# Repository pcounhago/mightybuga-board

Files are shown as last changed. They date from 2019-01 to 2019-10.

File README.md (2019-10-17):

# Mighty Bug-A Control board

Control board for the line follower racing car project designed at [A Industriosa](https://intranet.aindustriosa.org/).

## Releases

Version | Description | Status
------------ | ------------- | ------------
[v1](v1/README.md) | Initial board design. Has a mayor supply problem with the AMS1117-3.3 regulator. **Do not use unless you replace the regulator with a more capable one.** | Released
[v1.1](v1.1/README.md) | Updated version of v1 that solves the supply problems by replacing the regulator with a MP2307DN. | Released
[v2](v2/README.md) | Lighter version of the v1.1 redesigned to improve weight distribution in the car. | Released
[v2.1](v2.1/README.md) | Even lighter version of the control board. Include SWIO interface for programming and debug purposes. Fix some minor issues found in v2. | Released

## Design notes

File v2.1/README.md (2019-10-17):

# Mighty Bug-A Board v2.1

Control board for the line follower racing car project designed at [A Industriosa](https://intranet.aindustriosa.org/).

* Check the 3D printed chassis designs at [https://gitlab.com/punkto/line_follower_3d_designs](https://gitlab.com/punkto/line_follower_3d_designs)

* For the firmware refer to [https://github.com/hmightypirate/AllMyCircuits](https://github.com/hmightypirate/AllMyCircuits)

## Description

Designed to control a line follower racing car based on differential drive, this board includes an STM32F103 microcontroller coupled with a TB6612FNG dual channel motor driver and a U3V12F9 step-up regulator to power two Pololu micro metal gearmotors at stable 9V. The board provides headers to connect the motors using the magnetic encoder boards mounted on them.

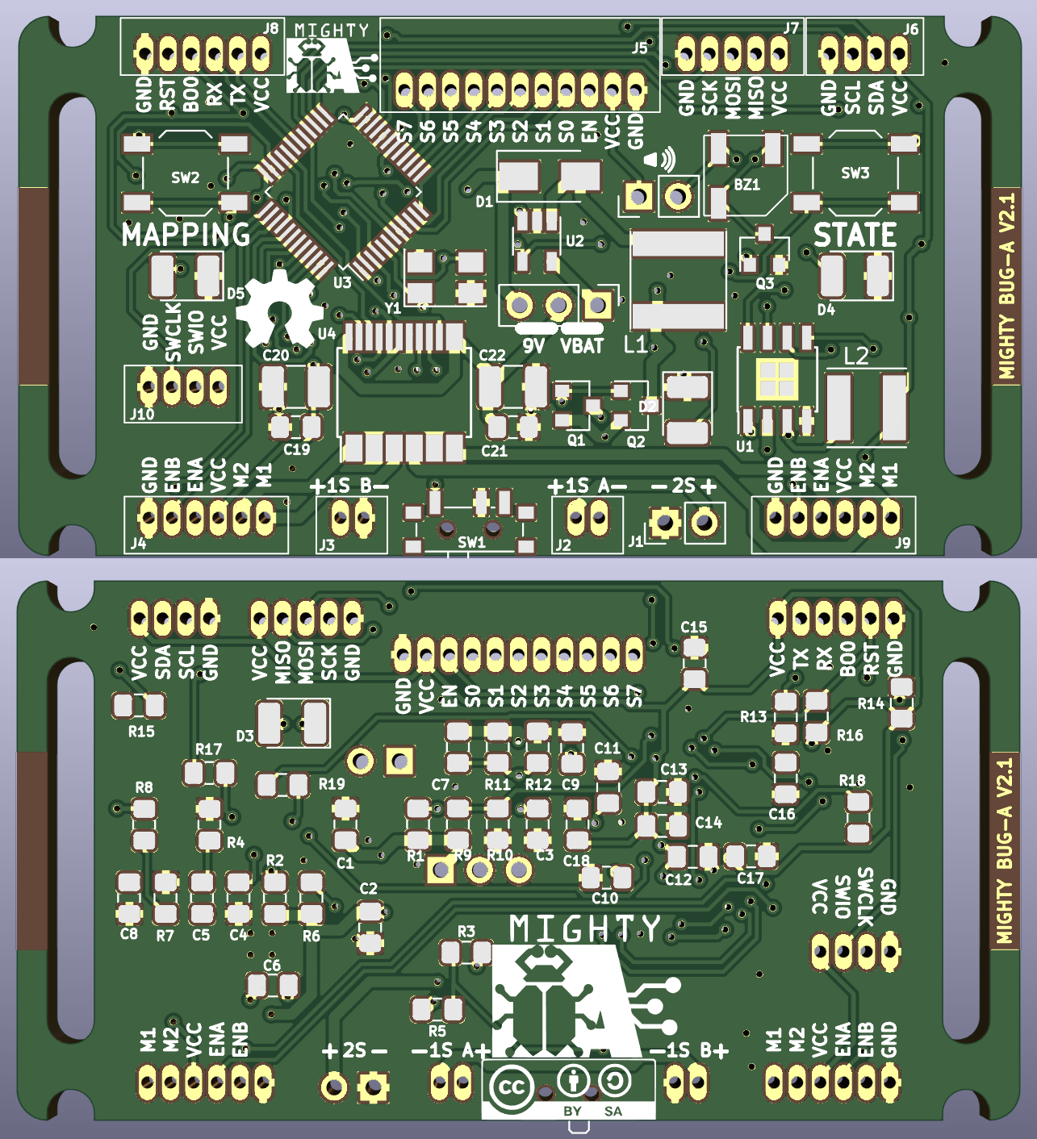
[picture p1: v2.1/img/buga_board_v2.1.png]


To detect the position of the line, a QTR-8A array featuring 8 Fairchild QRE1113 reflectance sensors is connected to the right angle header mounted on the front.

2 LEDs, 2 push buttons and a buzzer are provided to configure the board and give feedback while the car is on the track.

There is also a UART header that can be used to program the microcontroller and to establish a communication link through cable or Bluetooth if an HC-05 adapter is used.

To expand the capabilities of the board, I2C and SPI buses are available on a header so that other hardware (like an IMU or a slave microcontroller) can be added at any time.

## BOM

Reference | Description | Quantity
------------ | ------------- | ------------- |
BZ1 | MLT-5020 SMD buzzer | 1
C1, C14 | 0805 ceramic capacitor, 1uF | 2
C10, C11 | 0805 ceramic capacitor, 20pF | 2
C12, C13, C15, C16, C17, C19, C21 | 0805 ceramic capacitor, 100nF | 7
C2 | 0805 ceramic capacitor, 10uF | 1
C20, C22 | 0805 ceramic capacitor, 10uF | 2
C3 | 0805 ceramic capacitor, 56nF | 1
C4 | 0805 ceramic capacitor, 100pF | 1
C5 | 0805 ceramic capacitor, 3.9nF | 1
C6 | 10nF | 1
C7 | 15pF | 1
C8 | 22uF | 1
C9, C18 | 4.7uF | 2
D1 | B220A-13-F | 1
D2 | 1210 Green LED | 1
D3 | 1N4148 1210 diode | 1
D4 | 1210 Red LED | 1
D5 | 1210 Blue LED | 1
J1, JP2 | 2 pin 2.54mm vertical header | 2
J2, J6, J7 | JST B6B-ZR connector | 3
J3 | JST S11B-ZR | 1
J4 | JST B4B-ZR | 1
J5 | B5B-ZR | 1
JP1 | 3 pin 2.54mm straight header | 1
L1 | Taiyo Yuden_NR-60xx 4.7uH inductor | 1
L2 | Taiyo Yuden NR-50xx 10uH inductor | 1
Q1, Q2 | SI2369DS P-Channel 30V MOSFET, SOT-23 | 2
Q3 | S8050 NPN Transistor, SOT-23 | 1
R1, R6, R7, R9, R10, R13, R14, R15, R16, R19 | 0805 Resistor, 10k | 10
R11 | 0805 Resistor, 47k | 1
R12 | 0805 Resistor, 7.5k | 1
R17, R18 | 0805 Resistor, 100 | 2
R2, R3, R5, R20 | 0805 Resistor, 100K | 4
R4 | 0805 Resistor, 6.8k | 1
R8 | 0805 Resistor, 26.1k | 1
SW1 | PCM12 SPDT switch | 1
SW2, SW3 | TL3343 Push button | 2
U1 | MP2307DN | 1
U2 | SC4503 | 1
U3 | STM32F103C8T6 | 1
U4 | TB6612FNG | 1
Y1 | 5032 8Mhz crystal | 1

## Acknowledgements

This work was inspired by the great job done in the micromouse maze solving robot Bulebule by [Bulebots](https://github.com/Bulebots):

[https://github.com/Bulebots/bulebule](https://github.com/Bulebots/bulebule)

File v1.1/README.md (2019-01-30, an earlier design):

# Mighty Bug-A Board v1.1

Control board for the line follower racing car project designed at [A Industriosa](https://intranet.aindustriosa.org/).

* Check the 3D printed chassis designs at [https://gitlab.com/punkto/line_follower_3d_designs](https://gitlab.com/punkto/line_follower_3d_designs)

* For the firmware refer to [https://github.com/hmightypirate/AllMyCircuits](https://github.com/hmightypirate/AllMyCircuits)

## Description

Designed to control a line follower racing car based on differential drive, this board includes an STM32F103 microcontroller coupled with a TB6612FNG dual channel motor driver and a U3V12F9 step-up regulator to power two Pololu micro metal gearmotors at stable 9V. The board provides headers to connect the motors using the magnetic encoder boards mounted on them.

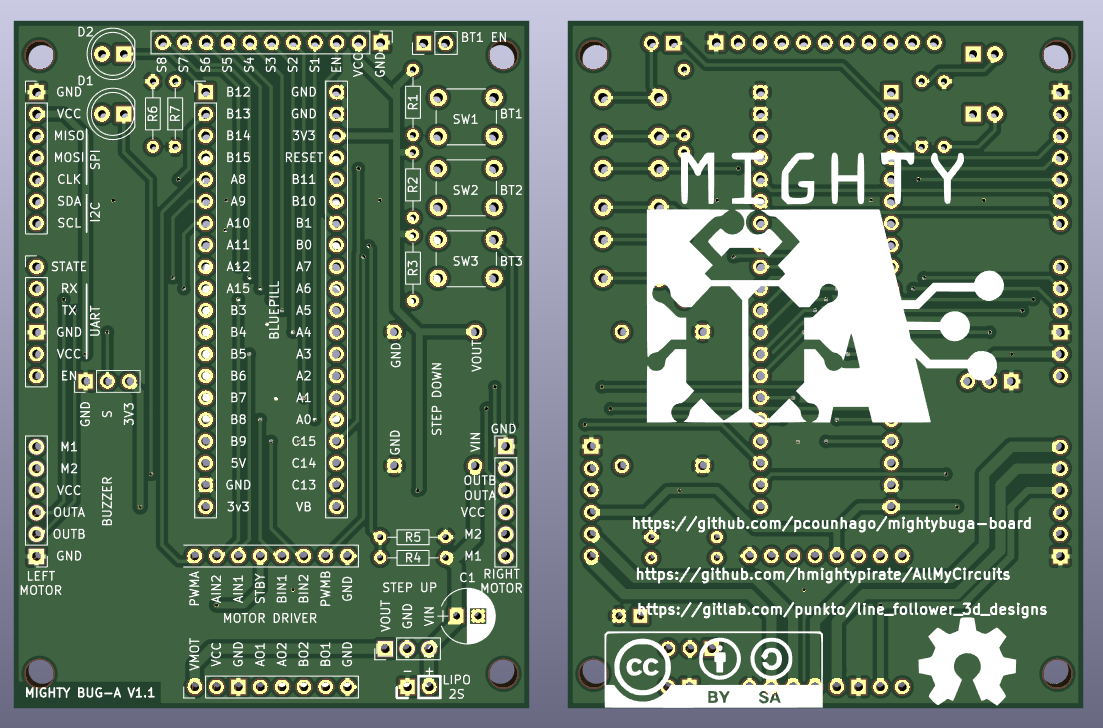
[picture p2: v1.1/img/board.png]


To detect the position of the line, a QTR-8A array featuring 8 Fairchild QRE1113 reflectance sensors is connected to the right angle header mounted on the front.

2 LEDs, 3 push buttons and a buzzer are provided to configure the board and give feedback while the car is on the track.

There is also a UART header that can be used to program the microcontroller and to establish a communication link through cable or Bluetooth if an HC-05 adapter is used.

To expand the capabilities of the board, I2C and SPI buses are available on a header so that other hardware (like an IMU or a slave microcontroller) can be added at any time.

**This board solves the problem with the regulator found in the previous version. By replacing the AMS1117-3.3 with a MP2307DN, the board can easily handle the regulation from the 8.4V provided by the battery when fully charged to the 3.3V required by the electronics.**

## BOM

Item | Description | Quantity
------------ | ------------- | ------------- |
Bluepill | STM32F103 microcontroller board | 1
MP2307DN | 3.3V Step-down voltage regulator. Can be found with the name Mini-360 in chinese stores. | 1
U3V12F9 | 9V Step-up regulator board from Pololu | 1
Buzzer | Passive buzzer board | 1
TB6612FNG | 2 Channel motor driver board | 1
5 mm LED | 5mm LEDs of different colors | 2
Push button | Through hole push buttons | 3
100Ω Resistor | Through hole resistors | 5
47kΩ Resistor | Through hole resistors | 1
20kΩ Resistor | Through hole resistors | 1
40x1 Female socket 2.54mm pitch | Female socket to plug, the bluepill, the motor driver and the Bluetooth module to the board | 1
40x1 Male pin 2.54mm pitch | Male pin strip to plug the motors, the battery, the expansion boards and the jumper to the board | 1
40x1 Right angle male pin 2.54mm pitch | Male pin strip to connect the reflectance sensor array to the board | 1
33uF Capacitor | Electrolytic capacitor to connect to the output of the step up regulator | 1

## Acknowledgements

This work was inspired by the great job done in the micromouse maze solving robot Bulebule by [Bulebots](https://github.com/Bulebots):

[https://github.com/Bulebots/bulebule](https://github.com/Bulebots/bulebule)

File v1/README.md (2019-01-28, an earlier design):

# Mighty Bug-A Board v1

Control board for the line follower racing car project designed at [A Industriosa](https://intranet.aindustriosa.org/).

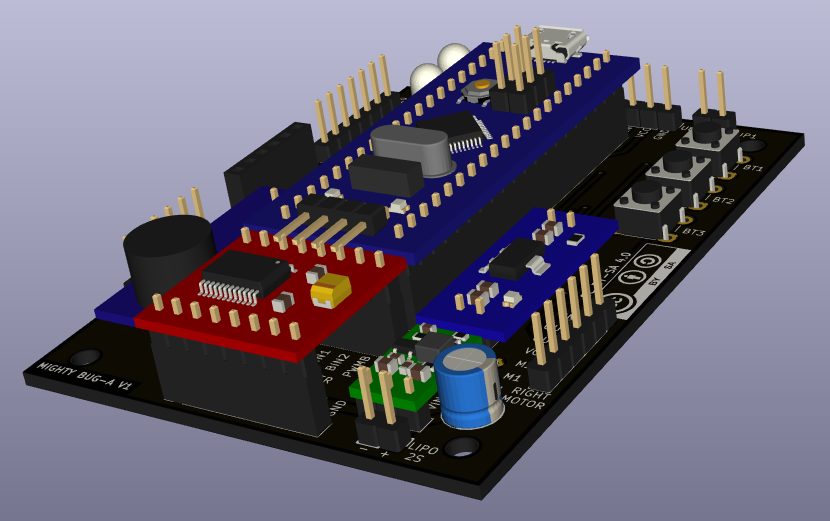
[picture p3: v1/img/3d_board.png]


* Check the 3D printed chassis designs at [https://gitlab.com/punkto/line_follower_3d_designs](https://gitlab.com/punkto/line_follower_3d_designs)

* For the firmware refer to [https://github.com/hmightypirate/AllMyCircuits](https://github.com/hmightypirate/AllMyCircuits)

## Warning!

**This board is made public here just for documentation purposes but its use in new designs is not recommended.** There is a major design flaw that makes the board burn when too much current is drawn. The step down regulator (AMS1117-3.3) can source up to 800 mA as stated in its datasheet. The problem is that the max output current is greatly affected by the difference between the input and output voltages. In this case The power source is a 2S lipo battery that provides 8.4V when fully charged. When converting this voltage down to 3.3V to power all the electronics, a lot of power is dissipated in the regulator making it burn when too much current is demanded.

**This issue is fixed in version v1.1 that can also be found in this repository.**

## Description

Designed to control a line follower racing car based on differential drive, this board includes an STM32F103 microcontroller coupled with a TB6612FNG dual channel motor driver and a U3V12F9 step-up regulator to power two Pololu micro metal gearmotors at stable 9V. The board provides headers to connect the motors using the magnetic encoder boards mounted on them.

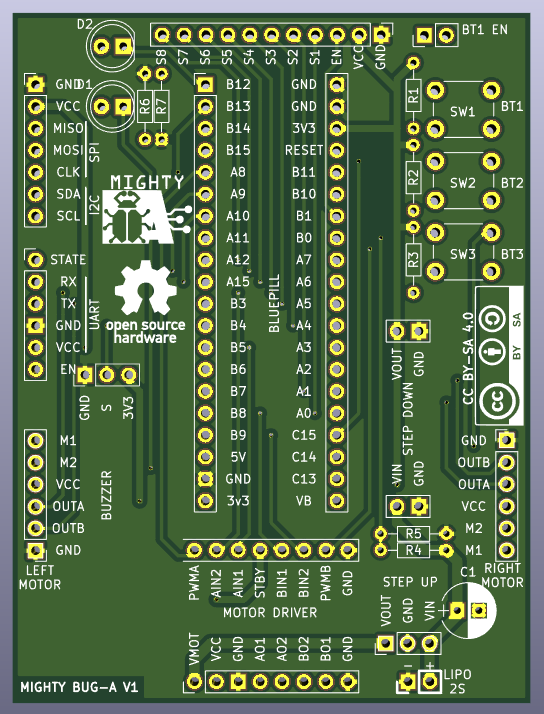
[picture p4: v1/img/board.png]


To detect the position of the line, a QTR-8A array featuring 8 Fairchild QRE1113 reflectance sensors is connected to the right angle header mounted on the front.

2 LEDs, 3 push buttons and a buzzer are provided to configure the board and give feedback while the car is on the track.

There is also a UART header that can be used to program the microcontroller and to establish a communication link through cable or Bluetooth if an HC-05 adapter is used.

To expand the capabilities of the board, I2C and SPI buses are available on a header so that other hardware (like an IMU or a slave microcontroller) can be added at any time.

## BOM

Item | Description | Quantity
------------ | ------------- | ------------- |
Bluepill | STM32F103 microcontroller board | 1
AMS1117-3.3 | 3.3V Step-down voltage regulator | 1
U3V12F9 | 9V Step-up regulator board from Pololu | 1
Buzzer | Passive buzzer board | 1
TB6612FNG | 2 Channel motor driver board | 1
5 mm LED | 5mm LEDs of different colors | 2
Push button | Through hole push buttons | 3
100Ω Resistor | Through hole resistors | 5
47kΩ Resistor | Through hole resistors | 1
20kΩ Resistor | Through hole resistors | 1
40x1 Female socket 2.54mm pitch | Female socket to plug, the bluepill, the motor driver and the Bluetooth module to the board | 1
40x1 Male pin 2.54mm pitch | Male pin strip to plug the motors, the battery, the expansion boards and the jumper to the board | 1
40x1 Right angle male pin 2.54mm pitch | Male pin strip to connect the reflectance sensor array to the board | 1
33uF Capacitor | Electrolytic capacitor to connect to the output of the step up regulator | 1

## Acknowledgements

This work was inspired by the great job done in the micromouse maze solving robot Bulebule by [Bulebots](https://github.com/Bulebots):

[https://github.com/Bulebots/bulebule](https://github.com/Bulebots/bulebule)

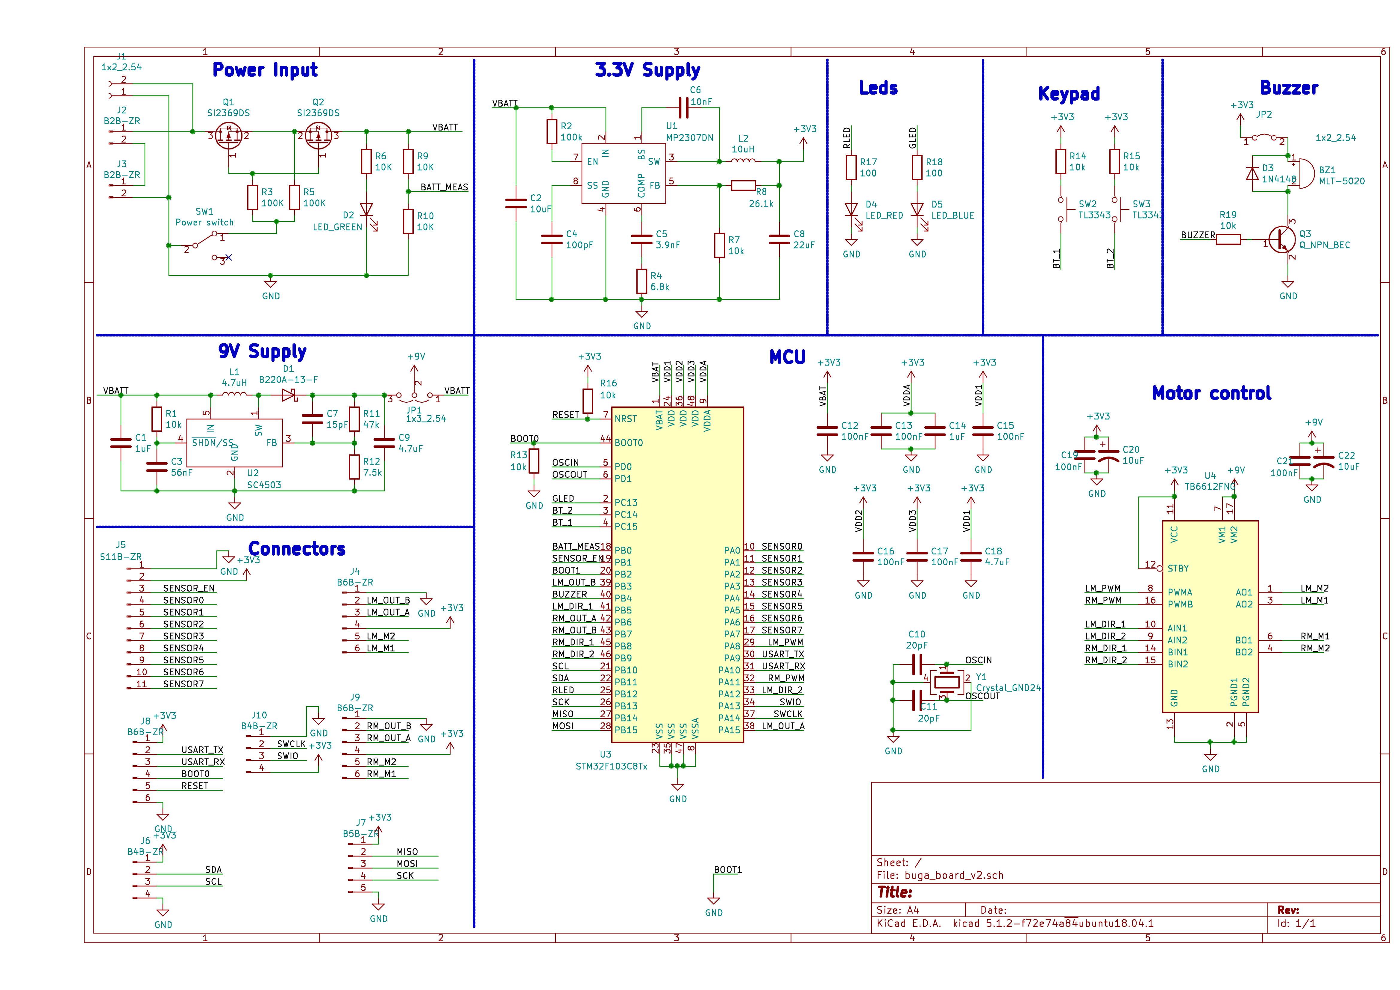
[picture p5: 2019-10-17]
v2.1/buga_board_v2-schematic.png

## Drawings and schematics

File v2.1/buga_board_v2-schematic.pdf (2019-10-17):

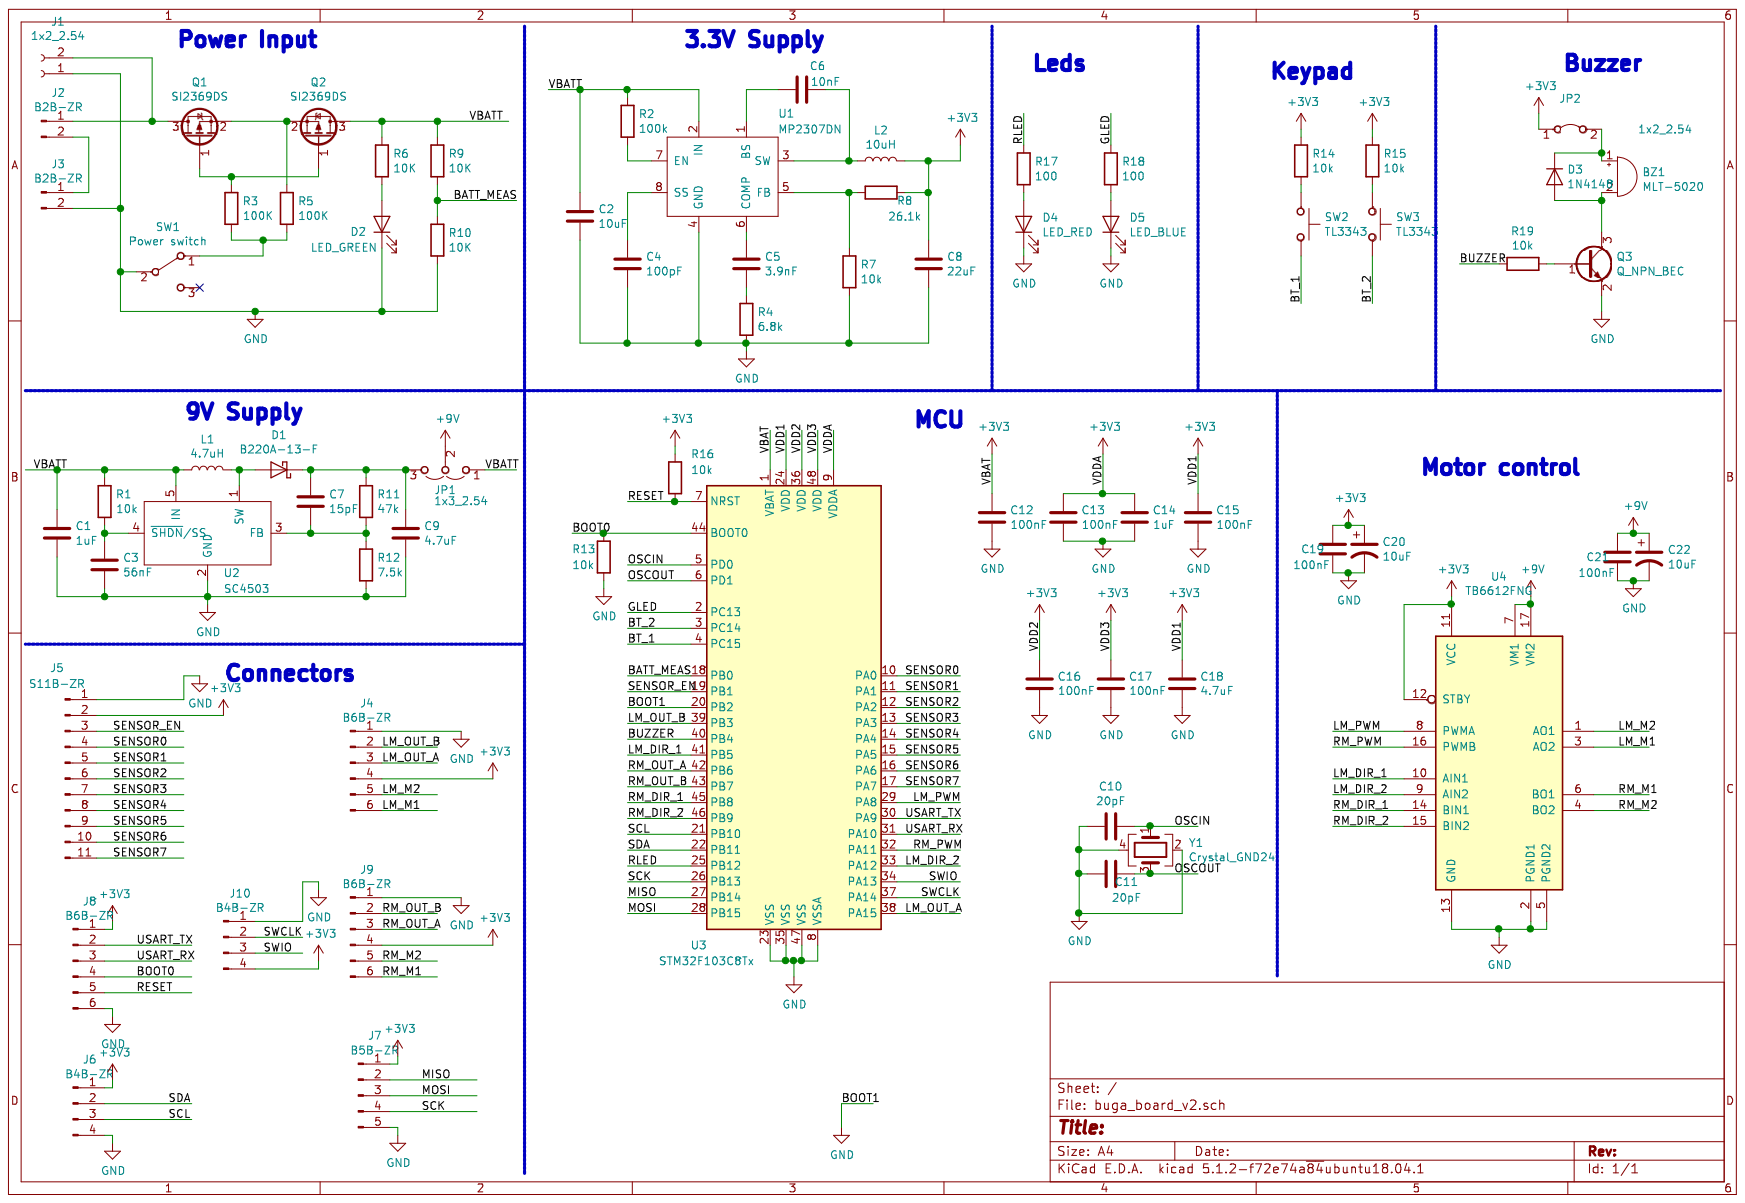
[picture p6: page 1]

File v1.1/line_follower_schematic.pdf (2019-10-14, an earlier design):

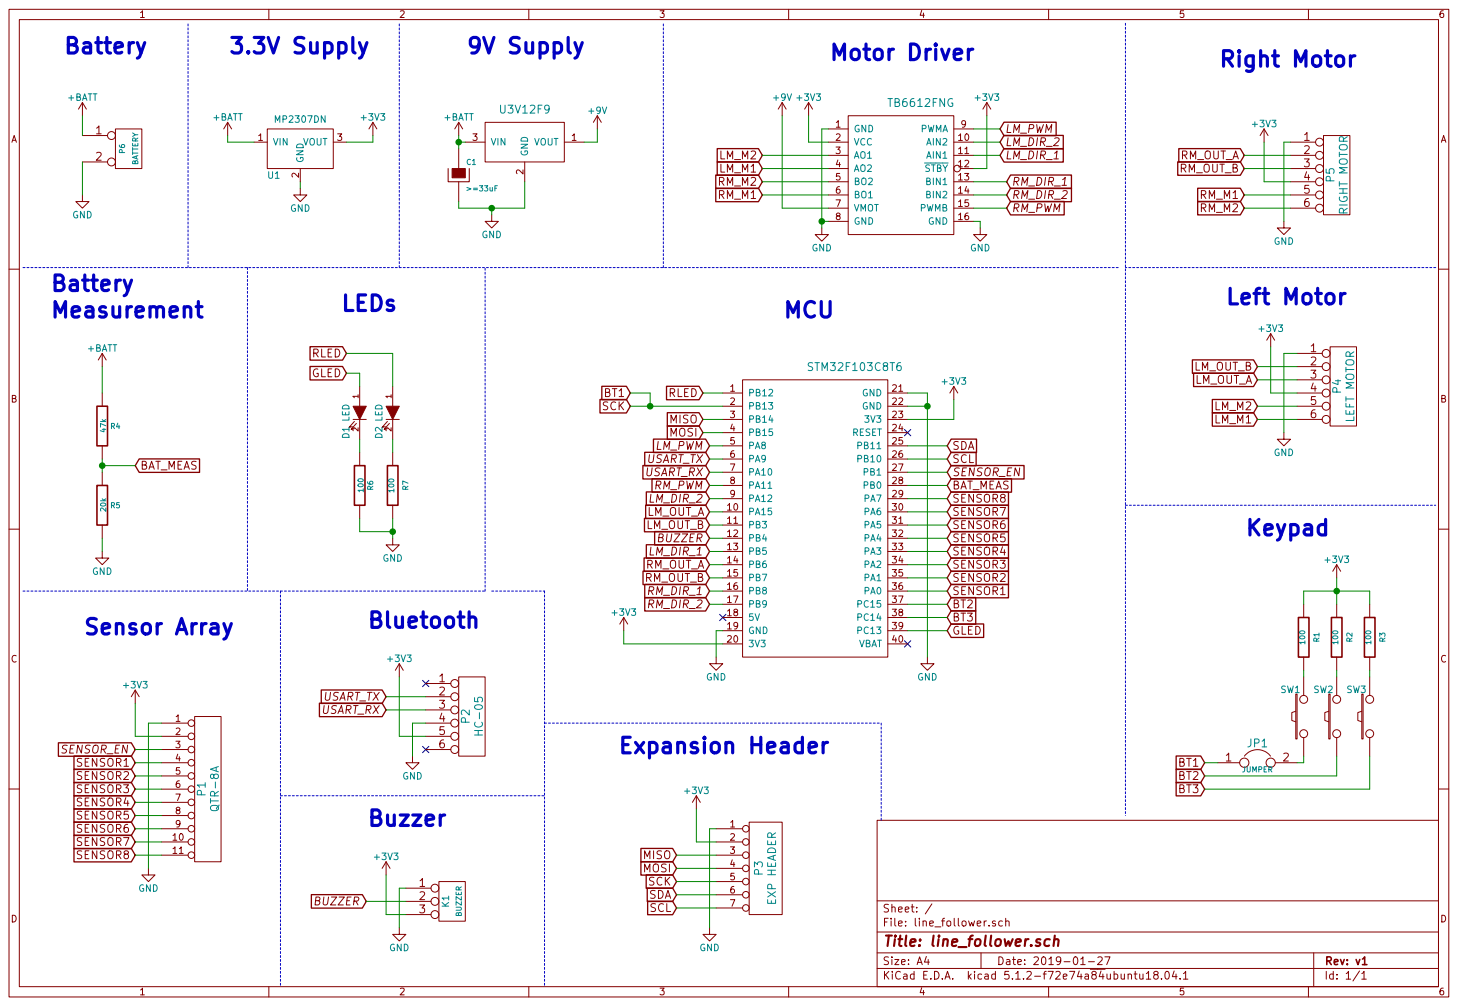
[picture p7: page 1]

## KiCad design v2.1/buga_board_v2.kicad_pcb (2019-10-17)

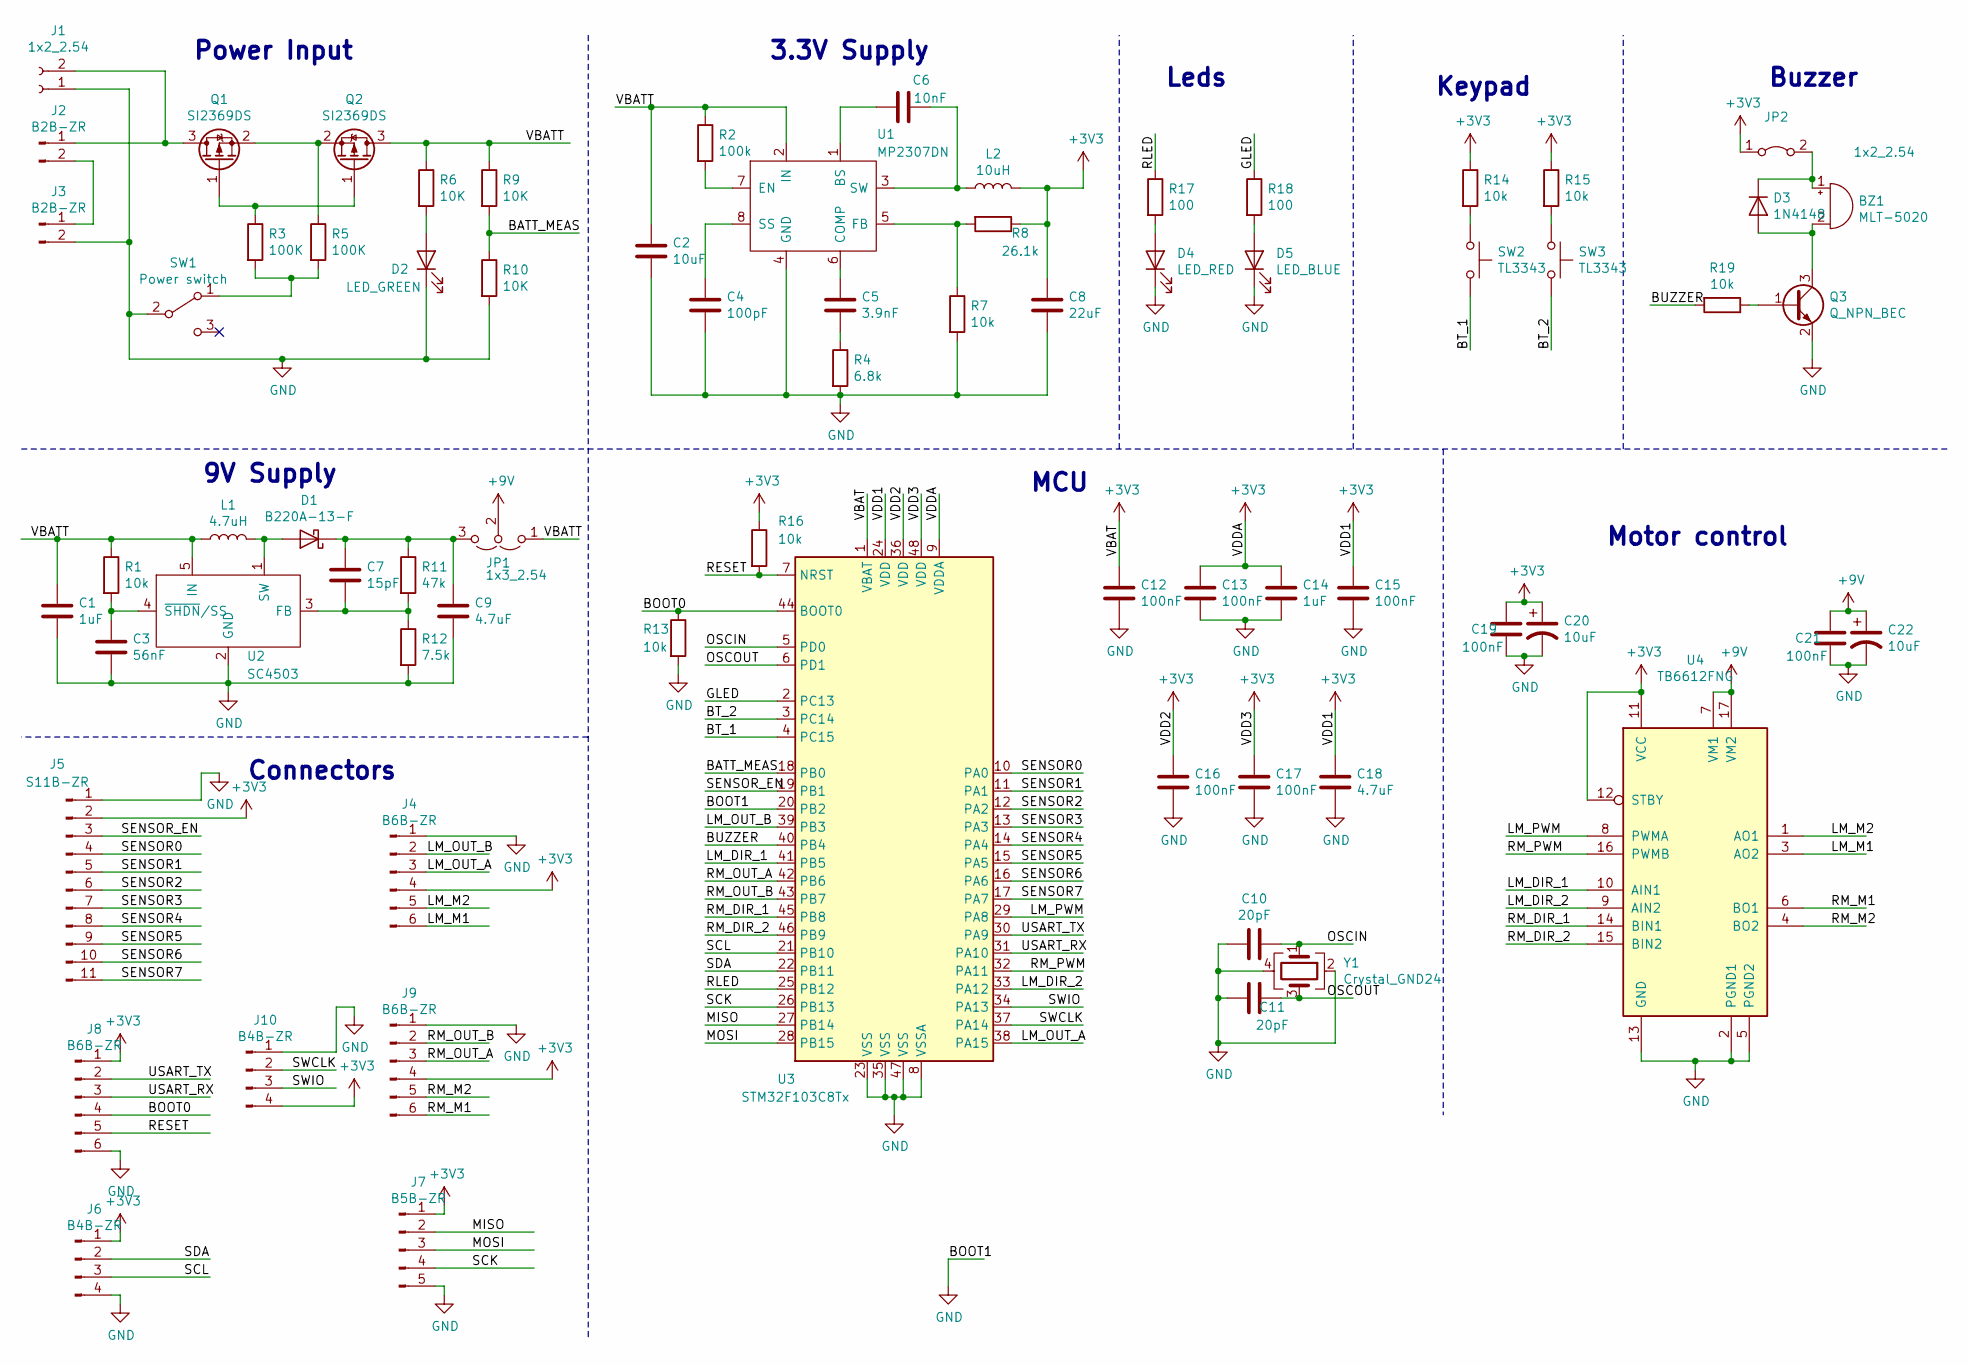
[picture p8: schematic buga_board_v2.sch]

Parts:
BZ1: MLT-5020
C1, C14: 1uF; C_0805_2012Metric_Pad1.15x1.40mm_HandSolder
C2: 10uF; C_0805_2012Metric_Pad1.15x1.40mm_HandSolder
C3: 56nF; C_0805_2012Metric_Pad1.15x1.40mm_HandSolder
C4: 100pF; C_0805_2012Metric_Pad1.15x1.40mm_HandSolder
C5: 3.9nF; C_0805_2012Metric_Pad1.15x1.40mm_HandSolder
C6: 10nF; C_0805_2012Metric_Pad1.15x1.40mm_HandSolder
C7: 15pF; C_0805_2012Metric_Pad1.15x1.40mm_HandSolder
C8: 22uF; C_0805_2012Metric_Pad1.15x1.40mm_HandSolder
C9, C18: 4.7uF; C_0805_2012Metric_Pad1.15x1.40mm_HandSolder
C10, C11: 20pF; C_0805_2012Metric_Pad1.15x1.40mm_HandSolder
C12, C13, C15, C16, C17, C19, C21: 100nF; C_0805_2012Metric_Pad1.15x1.40mm_HandSolder
C20, C22: 10uF; L_1210_3225Metric_Pad1.42x2.65mm_HandSolder
D1: B220A-13-F; D_SMA
D2: LED_GREEN; LED_1210_3225Metric_Pad1.42x2.65mm_HandSolder
D3: 1N4148; D_1210_3225Metric_Pad1.42x2.65mm_HandSolder
D4: LED_RED; LED_1210_3225Metric_Pad1.42x2.65mm_HandSolder
D5: LED_BLUE; LED_1210_3225Metric_Pad1.42x2.65mm_HandSolder
J1: 1x2_2.54; PinHeader_1x02_P2.54mm_Vertical
J2, J3: B2B-ZR
J4, J8, J9: B6B-ZR
J5: S11B-ZR
J6, J10: B4B-ZR
J7: B5B-ZR
JP1: 1x3_2.54; PinHeader_1x03_P2.54mm_Vertical
JP2: 1x2_2.54; PinHeader_1x02_P2.54mm_Vertical
L1: 4.7uH; L_Taiyo-Yuden_NR-60xx
L2: 10uH; L_Taiyo-Yuden_NR-50xx
Q1, Q2: SI2369DS; SOT-23
Q3: Q_NPN_BEC; SOT-23
R1, R7, R13, R14, R15, R16, R19: 10k; R_0805_2012Metric_Pad1.15x1.40mm_HandSolder
R2: 100k; R_0805_2012Metric_Pad1.15x1.40mm_HandSolder
R3, R5: 100K; R_0805_2012Metric_Pad1.15x1.40mm_HandSolder
R4: 6.8k; R_0805_2012Metric_Pad1.15x1.40mm_HandSolder
R6, R9, R10: 10K; R_0805_2012Metric_Pad1.15x1.40mm_HandSolder
R8: 26.1k; R_0805_2012Metric_Pad1.15x1.40mm_HandSolder
R11: 47k; R_0805_2012Metric_Pad1.15x1.40mm_HandSolder
R12: 7.5k; R_0805_2012Metric_Pad1.15x1.40mm_HandSolder
R17, R18: 100; R_0805_2012Metric_Pad1.15x1.40mm_HandSolder
SW1: Power switch; SW_SPDT_PCM12
SW2, SW3: TL3343; SW_SPST_TL3342
U1: MP2307DN; SOIC-8-1EP_3.9x4.9mm_P1.27mm_EP2.35x2.35mm
U2: SC4503; TSOT-23-5
U3: STM32F103C8Tx; LQFP-48_7x7mm_P0.5mm
U4: TB6612FNG; tb6612fng
Y1: Crystal_GND24; Crystal_SMD_5032-4Pin_5.0x3.2mm

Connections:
+3V3: C8.1, C12.1, C13.1, C14.1, C15.1, C16.1, C17.1, C18.1, C19.1, C20.1, J4.4, J5.2, J6.1, J7.1, J8.1, J9.4, J10.4, JP2.1 (A), L2.2, R8.1, R14.1, R15.1, R16.1, U3.1 (VBAT), U3.9 (VDDA), U3.24 (VDD), U3.36 (VDD), U3.48 (VDD), U4.11 (VCC), U4.12 (STBY)
+9V: C21.1, C22.1, JP1.2 (C), U4.7 (VM1), U4.17 (VM2)
/BATT_MEAS: R9.2, R10.1, U3.18 (PB0)
/BOOT0: J8.4, R13.1, U3.44 (BOOT0)
/BT_1: SW2.2, U3.4 (PC15)
/BT_2: SW3.2, U3.3 (PC14)
/BUZZER: R19.2, U3.40 (PB4)
/GLED: R18.1, U3.2 (PC13)
/LM_DIR_1: U3.41 (PB5), U4.10 (AIN1)
/LM_DIR_2: U3.33 (PA12), U4.9 (AIN2)
/LM_M1: J4.6, U4.3 (AO2)
/LM_M2: J4.5, U4.1 (AO1)
/LM_OUT_A: J4.3, U3.38 (PA15)
/LM_OUT_B: J4.2, U3.39 (PB3)
/LM_PWM: U3.29 (PA8), U4.8 (PWMA)
/MISO: J7.2, U3.27 (PB14)
/MOSI: J7.3, U3.28 (PB15)
/OSCIN: C10.1, U3.5 (PD0), Y1.1
/OSCOUT: C11.1, U3.6 (PD1), Y1.3
/RESET: J8.5, R16.2, U3.7 (NRST)
/RLED: R17.1, U3.25 (PB12)
/RM_DIR_1: U3.45 (PB8), U4.14 (BIN1)
/RM_DIR_2: U3.46 (PB9), U4.15 (BIN2)
/RM_M1: J9.6, U4.6 (BO1)
/RM_M2: J9.5, U4.4 (BO2)
/RM_OUT_A: J9.3, U3.42 (PB6)
/RM_OUT_B: J9.2, U3.43 (PB7)
/RM_PWM: U3.32 (PA11), U4.16 (PWMB)
/SCK: J7.4, U3.26 (PB13)
/SCL: J6.3, U3.21 (PB10)
/SDA: J6.2, U3.22 (PB11)
/SENSOR0: J5.4, U3.10 (PA0)
/SENSOR1: J5.5, U3.11 (PA1)
/SENSOR2: J5.6, U3.12 (PA2)
/SENSOR3: J5.7, U3.13 (PA3)
/SENSOR4: J5.8, U3.14 (PA4)
/SENSOR5: J5.9, U3.15 (PA5)
/SENSOR6: J5.10, U3.16 (PA6)
/SENSOR7: J5.11, U3.17 (PA7)
/SENSOR_EN: J5.3, U3.19 (PB1)
/SWCLK: J10.2, U3.37 (PA14)
/SWIO: J10.3, U3.34 (PA13)
/USART_RX: J8.3, U3.31 (PA10)
/USART_TX: J8.2, U3.30 (PA9)
/VBATT: C1.1, C2.1, JP1.1 (A), L1.1, Q2.3 (D), R1.1, R2.1, R6.1, R9.1, U1.2 (IN), U2.5 (IN)
GND: C1.2, C2.2, C3.2, C4.2, C8.2, C9.2, C10.2, C11.2, C12.2, C13.2, C14.2, C15.2, C16.2, C17.2, C18.2, C19.2, C20.2, C21.2, C22.2, D2.1 (K), D4.1 (K), D5.1 (K), J1.1, J3.2, J4.1, J5.1, J6.4, J7.5, J8.6, J9.1, J10.1, Q3.2 (E), R4.2, R7.2, R10.2, R12.2, R13.2, SW1.2 (B), U1.4 (GND), U2.2 (GND), U3.8 (VSSA), U3.20 (PB2), U3.23 (VSS), U3.35 (VSS), U3.47 (VSS), U4.2 (PGND1), U4.5 (PGND2), U4.13 (GND), Y1.2, Y1.4
unnamed: BZ1.1 (-), D3.1 (K), JP2.2 (B)
unnamed: BZ1.2 (+), D3.2 (A), Q3.3 (C)
unnamed: C3.1, R1.2, U2.4 (~SHDN~/SS)
unnamed: C4.1, U1.8 (SS)
unnamed: C5.1, U1.6 (COMP)
unnamed: C5.2, R4.1
unnamed: C6.1, L2.1, U1.3 (SW)
unnamed: C6.2, U1.1 (BS)
unnamed: C7.1, C9.1, D1.1 (K), JP1.3 (B), R11.1
unnamed: C7.2, R11.2, R12.1, U2.3 (FB)
unnamed: D1.2 (A), L1.2, U2.1 (SW)
unnamed: D2.2 (A), R6.2
unnamed: D4.2 (A), R17.2
unnamed: D5.2 (A), R18.2
unnamed: J1.2, J2.1, Q1.3 (D)
unnamed: J2.2, J3.1
unnamed: Q1.1 (G), Q2.1 (G), R3.1
unnamed: Q1.2 (S), Q2.2 (S), R5.1
unnamed: Q3.1 (B), R19.1
unnamed: R2.2, U1.7 (EN)
unnamed: R3.2, R5.2, SW1.1 (A)
unnamed: R7.1, R8.2, U1.5 (FB)
unnamed: R14.2, SW2.1
unnamed: R15.2, SW3.1

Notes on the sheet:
Power Input
9V Supply
3.3V Supply
Motor control
Buzzer
Keypad
Leds
MCU
Connectors

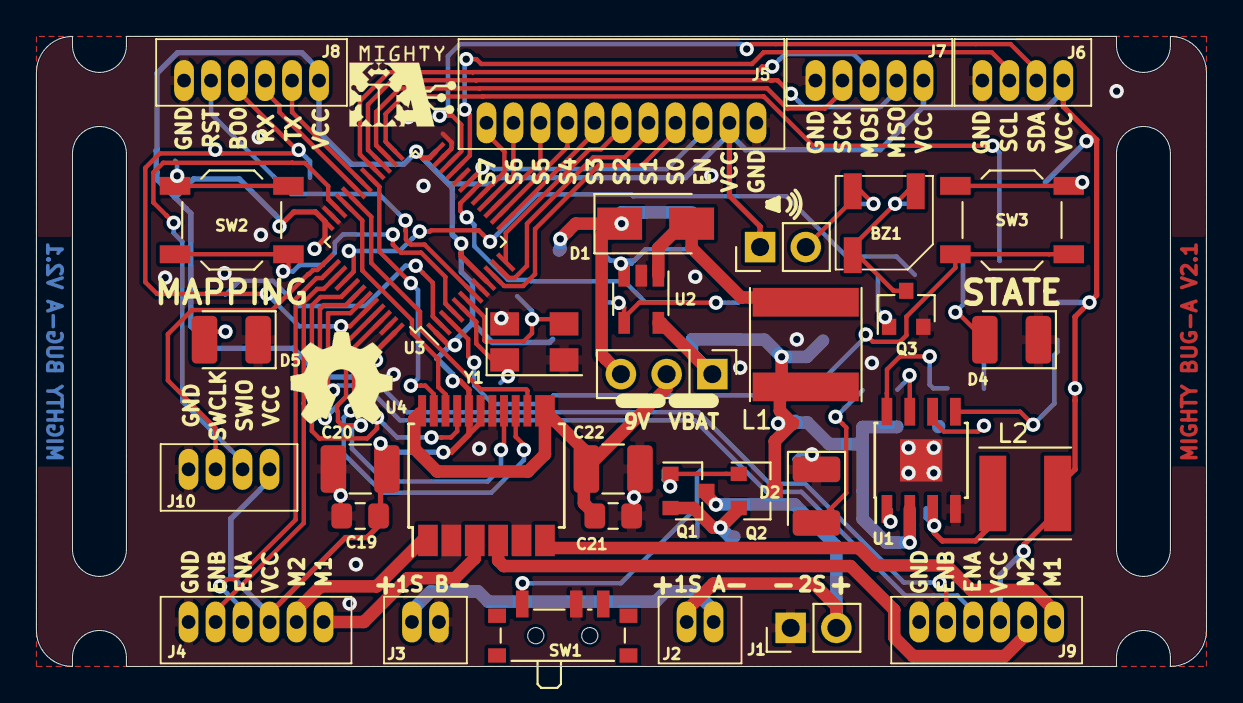
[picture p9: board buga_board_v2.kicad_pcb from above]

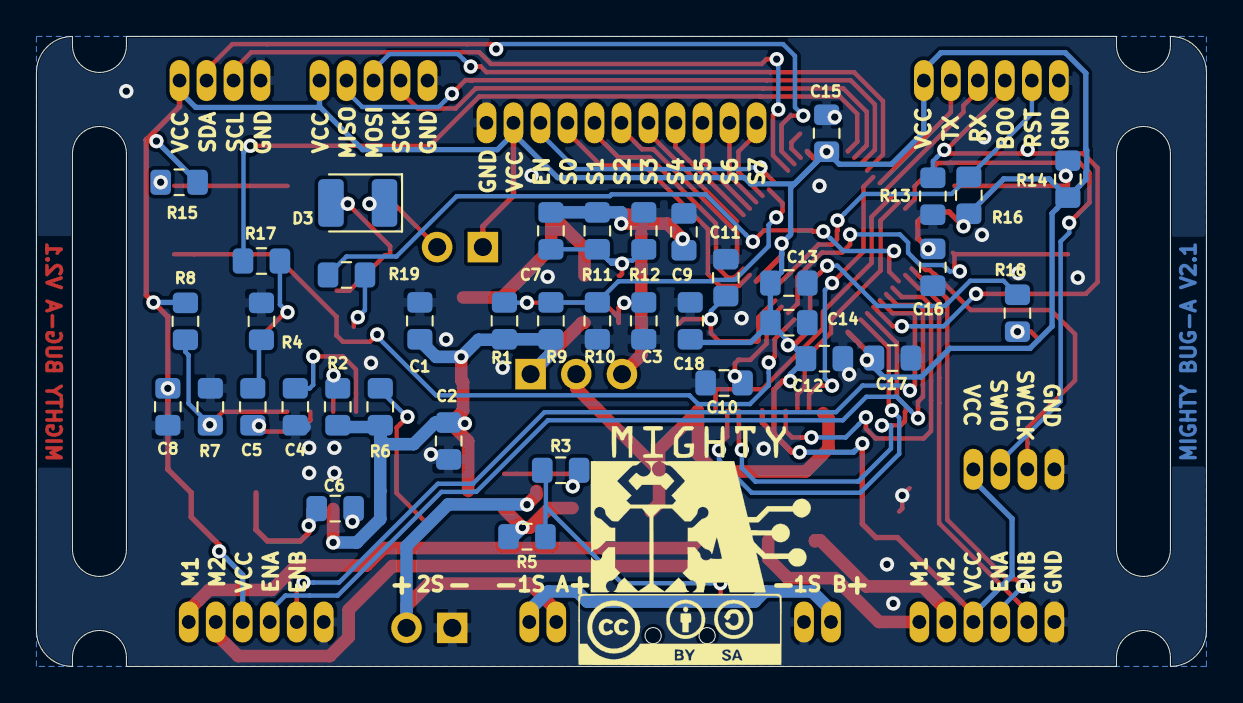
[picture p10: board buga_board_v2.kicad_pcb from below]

Board: 2 copper layers, 65.0 x 35.0 mm, 72 parts (38 on the bottom side), 70 nets.

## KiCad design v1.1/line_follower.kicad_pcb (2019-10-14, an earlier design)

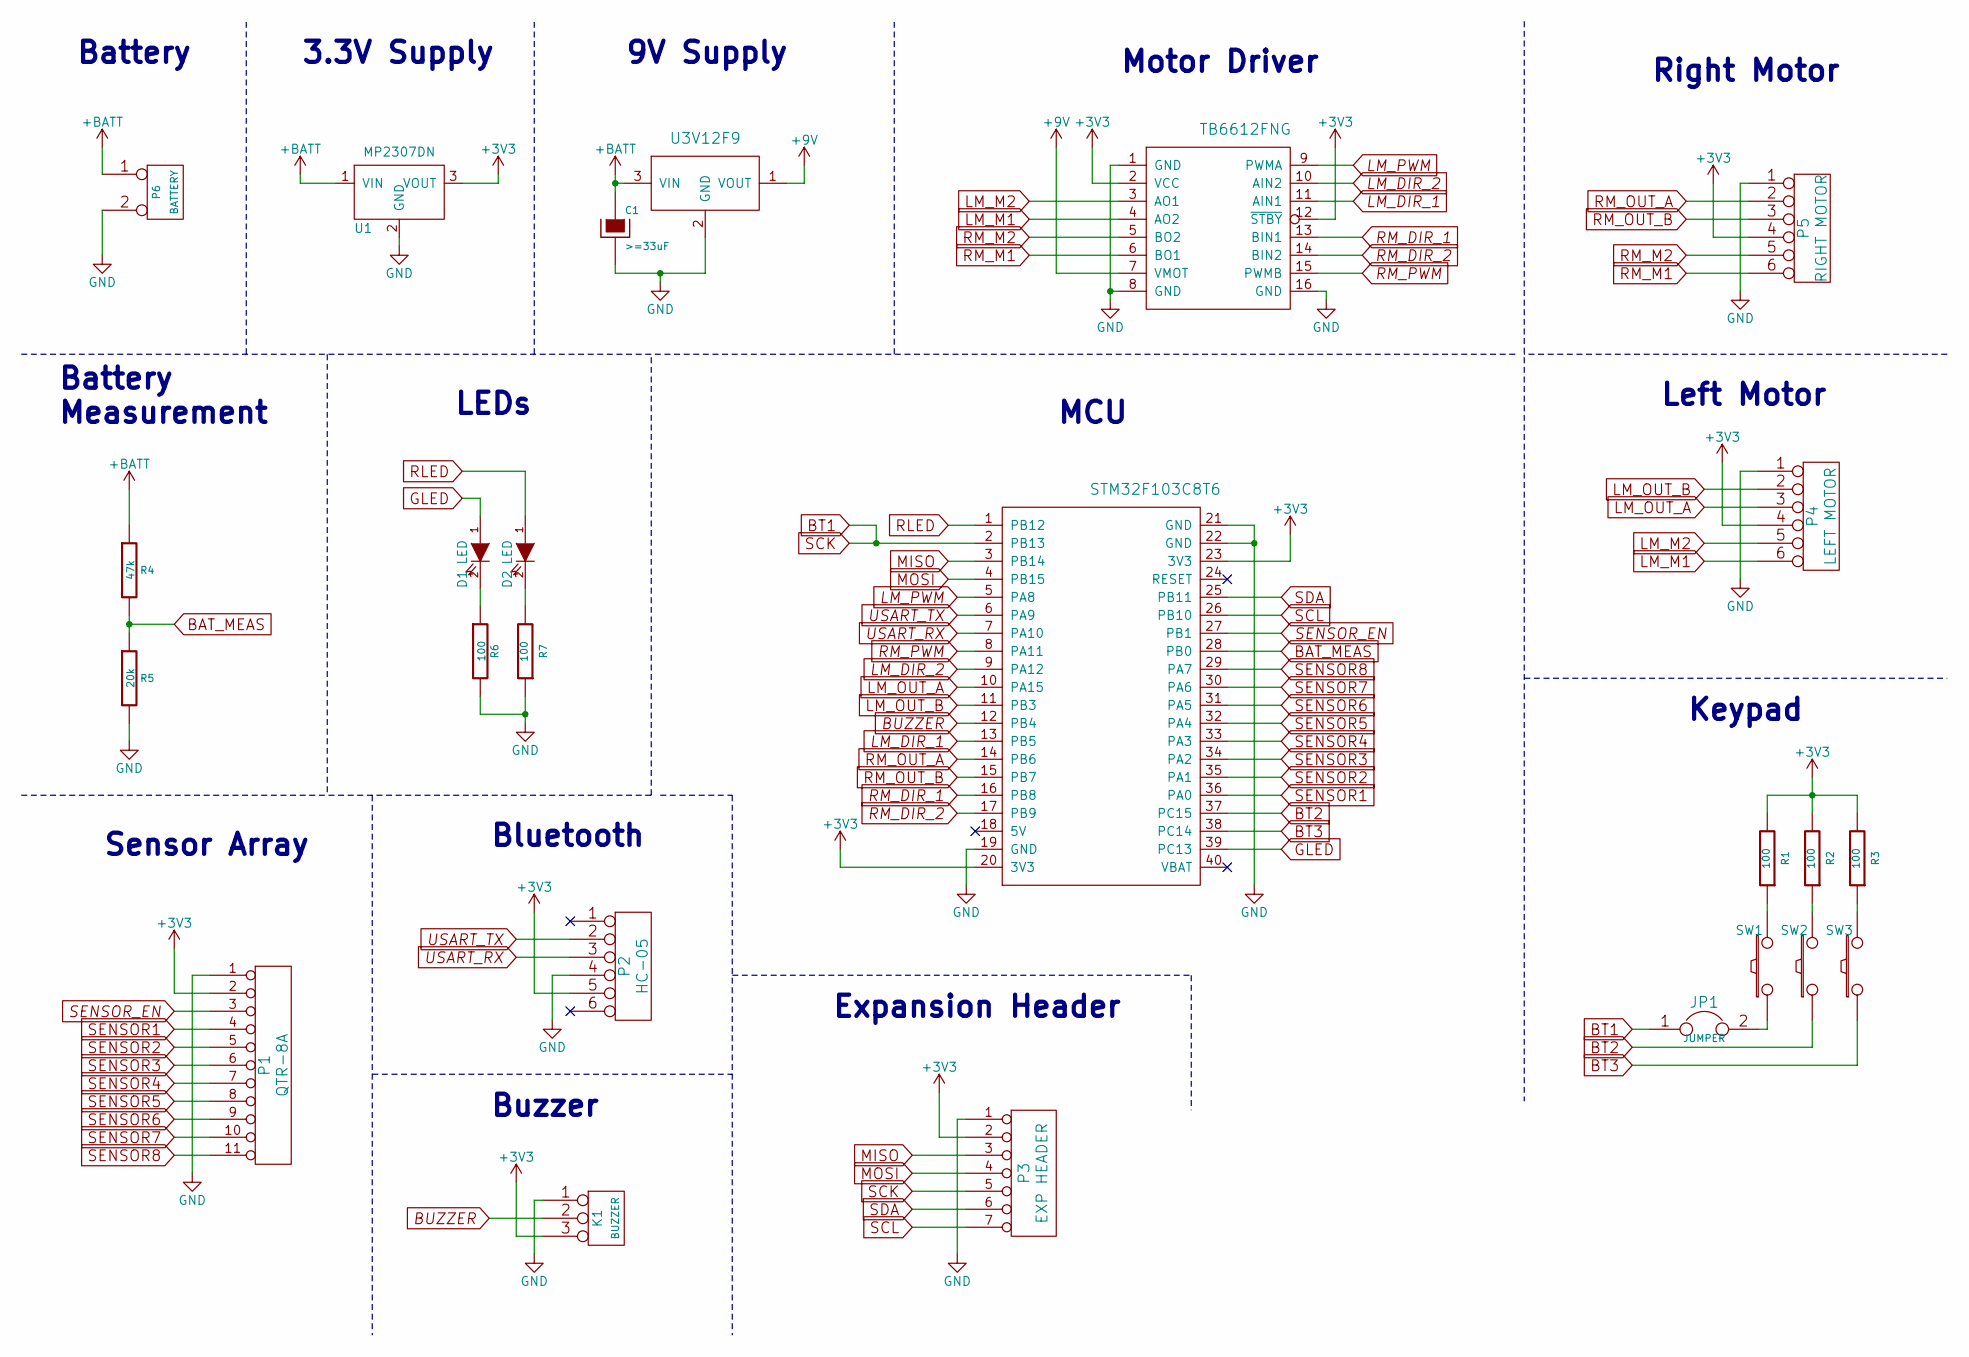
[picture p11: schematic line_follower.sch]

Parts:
C1: >=33uF; CP_Radial_D6.3mm_P2.50mm
D1, D2: LED; LED_D5.0mm
JP1: JUMPER; Pin_Header_Straight_1x02_Pitch2.54mm
K1: BUZZER; Buzzer
P1: QTR-8A; Pin_Header_Straight_1x11_Pitch2.54mm
P2: HC-05
P3: EXP HEADER; Header
P4: LEFT MOTOR; pololu_magnetic_encoder
P5: RIGHT MOTOR; pololu_magnetic_encoder
P6: BATTERY; 2S_LiPo
R1, R2, R3, R6, R7: 100; R_Axial_DIN0204_L3.6mm_D1.6mm_P7.62mm_Horizontal
R4: 47k; R_Axial_DIN0204_L3.6mm_D1.6mm_P7.62mm_Horizontal
R5: 20k; R_Axial_DIN0204_L3.6mm_D1.6mm_P7.62mm_Horizontal
SW1, SW2, SW3: SW_PUSH; SW_PUSH_6mm_h5mm
U1: MP2307DN
U2: U3V12F9; u3v12f9
U6: STM32F103C8T6; BluePill_STM32F103C
U7: TB6612FNG; tb6612fng_sparkfun

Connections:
+3V3: K1.3, P1.2, P2.5, P3.2, P4.4, P5.4, R1.2, R2.2, R3.2, U1.3 (VOUT), U6.20 (3V3), U6.23 (3V3), U7.2 (VCC), U7.12 (~STBY~)
+9V: U2.1 (VOUT), U7.7 (VMOT)
+BATT: C1.1, P6.1, R4.1, U1.1 (VIN), U2.3 (VIN)
BAT_MEAS: R4.2, R5.1, U6.28 (PB0)
BT1: JP1.1, P3.5, U6.2 (PB13)
BT2: SW2.1, U6.37 (PC15)
BT3: SW3.1, U6.38 (PC14)
BUZZER: K1.2 (PM), U6.12 (PB4)
GLED: D1.1 (A), U6.39 (PC13)
GND: C1.2, K1.1, P1.1, P2.4, P3.1, P4.1, P5.1, P6.2 (PM), R5.2, R6.2, R7.1, U1.2 (GND), U2.2 (GND), U6.19 (GND), U6.21 (GND), U6.22 (GND), U7.1 (GND), U7.8 (GND), U7.16 (GND)
LM_DIR_1: U6.13 (PB5), U7.11 (AIN1)
LM_DIR_2: U6.9 (PA12), U7.10 (AIN2)
LM_M1: P4.5, U7.3 (AO1)
LM_M2: P4.6, U7.4 (AO2)
LM_OUT_A: P4.3, U6.10 (PA15)
LM_OUT_B: P4.2, U6.11 (PB3)
LM_PWM: U6.5 (PA8), U7.9 (PWMA)
MISO: P3.3, U6.3 (PB14)
MOSI: P3.4, U6.4 (PB15)
unnamed: D1.2 (K), R6.1
unnamed: D2.2 (K), R7.2
unnamed: JP1.2, SW1.1
unnamed: R1.1, SW1.2
unnamed: R2.1, SW2.2
unnamed: R3.1, SW3.2
RLED: D2.1 (A), U6.1 (PB12)
RM_DIR_1: U6.16 (PB8), U7.13 (BIN1)
RM_DIR_2: U6.17 (PB9), U7.14 (BIN2)
RM_M1: P5.5, U7.5 (BO2)
RM_M2: P5.6, U7.6 (BO1)
RM_OUT_A: P5.2, U6.14 (PB6)
RM_OUT_B: P5.3, U6.15 (PB7)
RM_PWM: U6.8 (PA11), U7.15 (PWMB)
SCL: P3.7, U6.26 (PB10)
SDA: P3.6, U6.25 (PB11)
SENSOR1: P1.4, U6.36 (PA0)
SENSOR2: P1.5, U6.35 (PA1)
SENSOR3: P1.6, U6.34 (PA2)
SENSOR4: P1.7, U6.33 (PA3)
SENSOR5: P1.8, U6.32 (PA4)
SENSOR6: P1.9, U6.31 (PA5)
SENSOR7: P1.10, U6.30 (PA6)
SENSOR8: P1.11, U6.29 (PA7)
SENSOR_EN: P1.3, U6.27 (PB1)
USART_RX: P2.3, U6.7 (PA10)
USART_TX: P2.2, U6.6 (PA9)

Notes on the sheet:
Right Motor
Left Motor
Motor Driver
Keypad
9V Supply
3.3V Supply
Battery
Battery Measurement
LEDs
Sensor Array
Bluetooth
Buzzer
Expansion Header
MCU

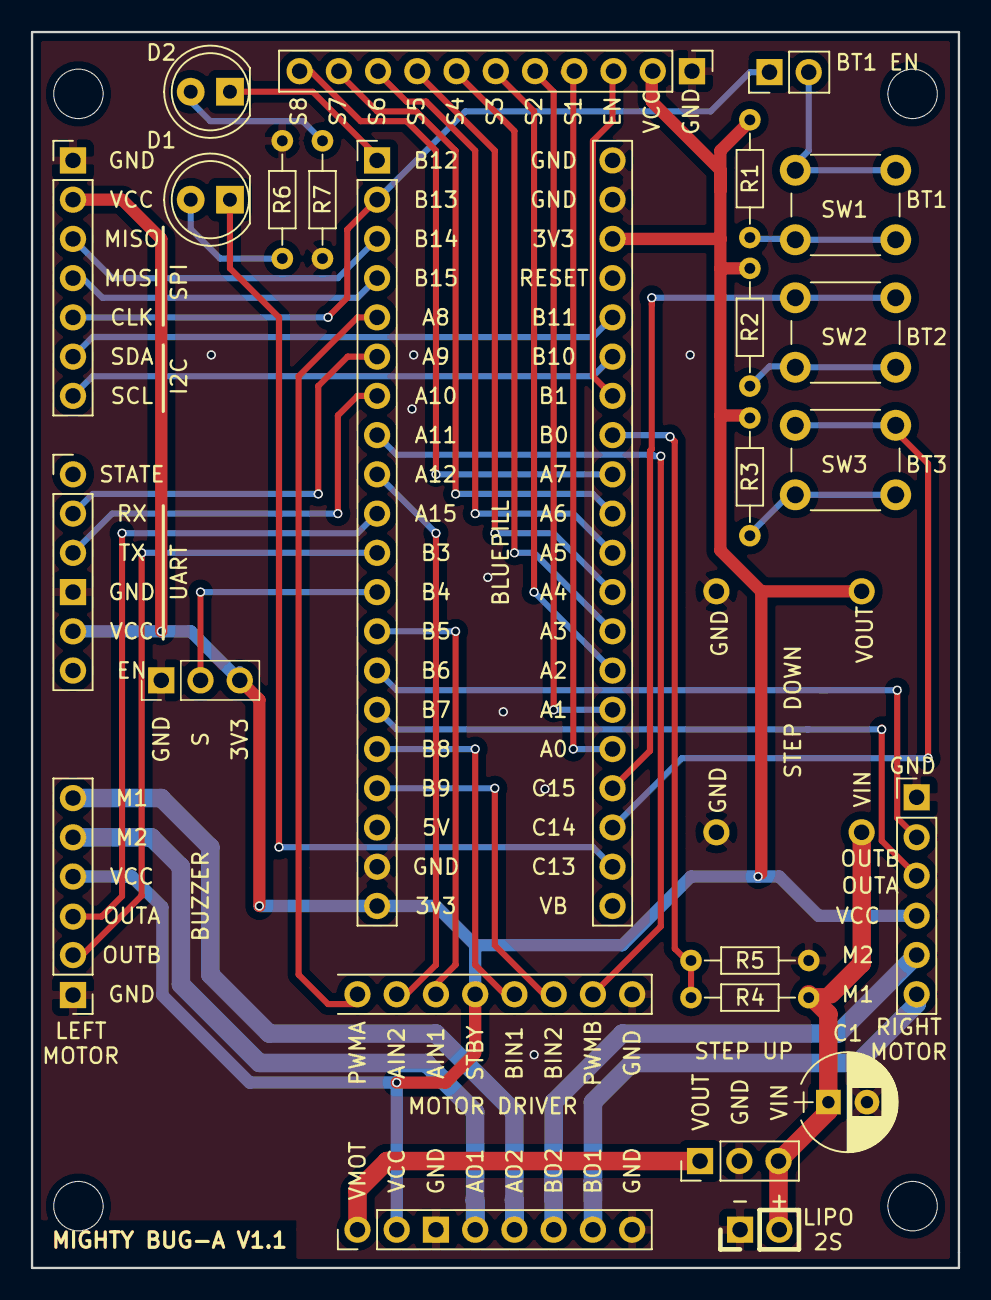
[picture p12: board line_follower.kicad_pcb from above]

Board: 2 copper layers, 60.0 x 80.0 mm, 25 parts (0 on the bottom side), 46 nets.

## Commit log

2019-01-28 Add board v1 to the repository
    [line_follower.kicad_pcb, line_follower.sch]
2019-01-29 Add missing graphics and mounting holes
    [line_follower.kicad_pcb]
2019-01-30 Add board version v1.1
    [line_follower.kicad_pcb, line_follower.sch]
2019-10-14 Small cosmetic changes. Include schematic in PNG format.
    [line_follower.kicad_pcb, line_follower.sch]
2019-10-14 Add schematic in PNG format for v1 board.
2019-10-16 Release V2 board
    [buga_board_v2.kicad_pcb, buga_board_v2.sch]
2019-10-17 Release v2.1 board
    [buga_board_v2.kicad_pcb, buga_board_v2.sch]

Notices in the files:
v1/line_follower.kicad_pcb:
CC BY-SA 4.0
